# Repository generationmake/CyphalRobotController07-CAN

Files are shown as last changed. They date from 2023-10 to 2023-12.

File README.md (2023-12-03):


CyphalRobotController07/CAN
==================
Main controller board for the T07 robot platform and similar robots with a Raspberry Pi Pico to connect via CAN using OpenCyphal and UCANPHY Micro 

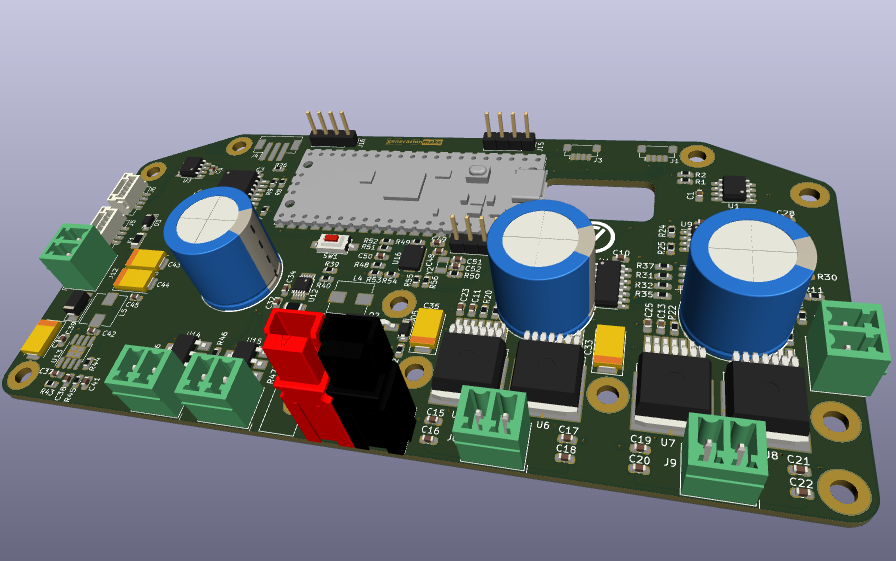
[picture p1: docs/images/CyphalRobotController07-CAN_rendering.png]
CyphalRobotController07/CAN rendering


## features

- power supply for the whole system
  - 5 V for the cyphal network and embedded board (Raspberry Pi or Beagle Bone Black)
  - switchable output of battery voltage to supply additional hardware
  - switchable output of battery voltage to supply LED or head lamp
  - Input voltage up to 25 V
  - Blade type fuse (ATO fuse)
  - Power Pole connector
  - measurement of input voltage and current with TI INA226
- control 2 DC motors
  - 2 quad encoders for motors
  - emergency stop
  - Infineon IFX007T drivers, up to 40V and 55A
- ~~3 ultra sonic sensors HC-SR04~~ (not implemented yet)
- I2C bus
  - qwiic connector
  - 9 axis IMU Bosch BNO055 via I2C
  - back-EMF measurement with ADS1015
  - EEPROM 24LC64
- serial port for optional GNSS
- Neopixel for status
- CAN with Cyphal support

## Firmware
* [CyphalRobotController07-CAN-firmware](https://github.com/107-systems/CyphalRobotController07-CAN-firmware): This is the default firmware for this board. It enables all basic functions

## Pin Usage

### Raspberry Pi Pico (CN1)

| **Pin** | **Pin Name** | **Signal** | **Direction** | **Description** |
|:---:|:---:|:---:|:---:|:---:|
| 1 | GP0 | UART0_TX | output | reserved for future use (GNSS) |
| 2 | GP1 | UART0_RX | input | reserved for future use (GNSS) |
| 3 | GND | GND | GND | |
| 4 | GP2 | QUAD0 | input | Quad encoder A channel 0 |
| 5 | GP3 | QUAD1 | input | Quad encoder A channel 1 |
| 6 | GP4 | I2C0_SDA | bidir | for eeprom and qwiic connector |
| 7 | GP5 | I2C0_SCL | output | for eeprom and qwiic connector |
| 8 | GND | GND | GND | |
| 9 | GP6 | PWM4 | output | motor pwm output 4 |
| 10 | GP7 | PWM3 | output | motor pwm output 3 |
| 11 | GP8 | PWM2 | output | motor pwm output 2 |
| 12 | GP9 | PWM1 | output | motor pwm output 1 |
| 13 | GND | GND | GND | |
| 14 | GP10 | INH34 | output | motor inhibit output 3 and 4 |
| 15 | GP11 | INH12 | output | motor inhibit output 1 and 2 |
| 16 | GP12 | EM_STOP | input | emergency stop |
| 17 | GP13 | NEOPIXEL | output | Neopixel |
| 18 | GND | GND | GND | |
| 19 | GP14 | QUAD2 | input | Quad encoder B channel 0 |
| 20 | GP15 | QUAD3 | input | Quad encoder B channel 1 |
| 21 | GP16 | SPI_MISO | input | SPI for MCP2515 |
| 22 | GP17 | MCP2515_CS | output | SPI for MCP2515 |
| 23 | GND | GND | GND | |
| 24 | GP18 | SPI_CLK | output | SPI for MCP2515 |
| 25 | GP19 | SPI_MOSI | output | SPI for MCP2515 |
| 26 | GP20 | MCP2515_INT | input | interrupt for MCP2515 |
| 27 | GP21 | OUTPUT0 | output | power output 0 |
| 28 | GND | GND | GND | |
| 29 | GP22 | OUTPUT1 | output | power output 1 |
| 30 | RUN | RESET | input | Reset for Board |
| 31 | GP26 | ANALOG_INPUT0 | analog input  | analog input 0 |
| 32 | GP27 | ANALOG_INPUT1 | analog input  | analog input 1 |
| 33 | GND | GND | GND | |
| 34 | GP28 | ANALOG_INPUT2 | analog input  | analog input 2 |
| 35 | ADC_VREF | | analog | |
| 36 | 3V3 (OUT) | 3V3-rail | power | supply voltage for board |
| 37 | 3V3_EN | | input | |
| 38 | GND | GND | GND | |
| 39 | VSYS | | power | |
| 40 | VBUS | 5V-rail | power | supply voltage for board |

## I2C devices

| address | device  | description |
|---|---|---|
| 0x40 | INA226  | voltage and current measurement |
| 0x48 | ADS1015 | motor measurement |
| 0x4A | BNO055  | IMU |
| 0x50 | 24LC64  | eeprom for storage of settings  |
## PCB

### Top

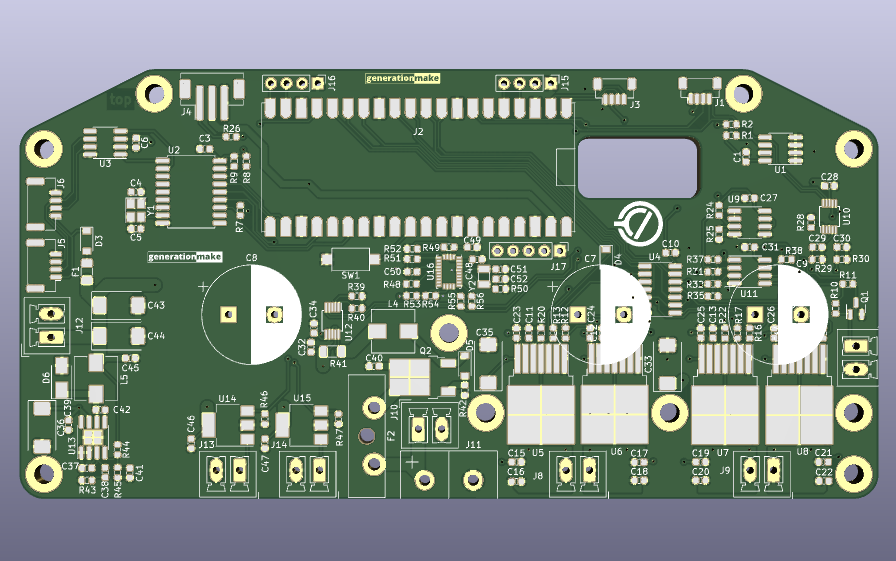
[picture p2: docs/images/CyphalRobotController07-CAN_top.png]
CyphalRobotController07/CAN PCB top


### Bottom

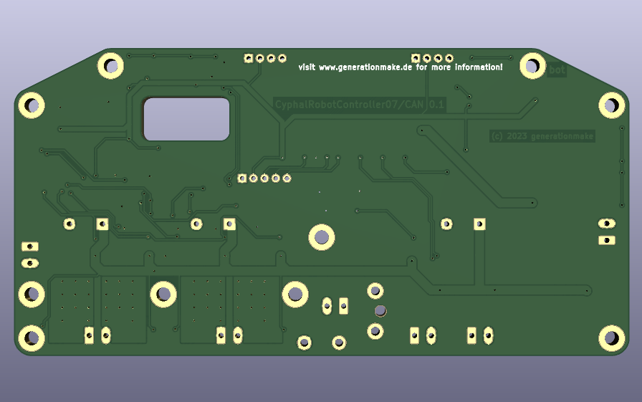
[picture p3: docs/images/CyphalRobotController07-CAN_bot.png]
CyphalRobotController07/CAN PCB bot


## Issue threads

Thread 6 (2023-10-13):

replace tantal capacitors with electrolytic capacitors

generationmake, 2023-10-13:
cheaper and better availability

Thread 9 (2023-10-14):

fix hardware errors of pcb 0.1

generationmake, 2023-10-14:

generationmake, 2023-10-15:
connect both 3.3 v rails

generationmake, 2023-10-15:
add weak pull down (100k) on EM_STOP_D

generationmake, 2023-11-16:
add always on output for battery voltage to connect external controller board

Closed 2025-09-04.

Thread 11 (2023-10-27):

Feature Request: Adjust footprint to allow usage Rasperry Pi Pico w/ Pin Headers (RP  PICO H)

aentinger, 2023-10-27:
See this [one](https://www.conrad.at/de/p/raspberry-pi-rp-pico-h-mikrocontroller-rp-pico-h-2615362.html).

I mistakenly ordered 20 pieces of that one ... 🤦

Closed 2025-09-04.

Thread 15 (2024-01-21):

update input voltage to 40 V

generationmake, 2024-01-21:
to allow usage of 40 V power tool batteries or 2x 20 V in series

generationmake, 2024-01-21:
replace INA226
check capacitors

generationmake, 2024-01-21:
replace ITS4200S

generationmake, 2024-01-21:
replace IPD90P03P4L-04 with IPD90P04P4L-04

Closed 2025-09-04.

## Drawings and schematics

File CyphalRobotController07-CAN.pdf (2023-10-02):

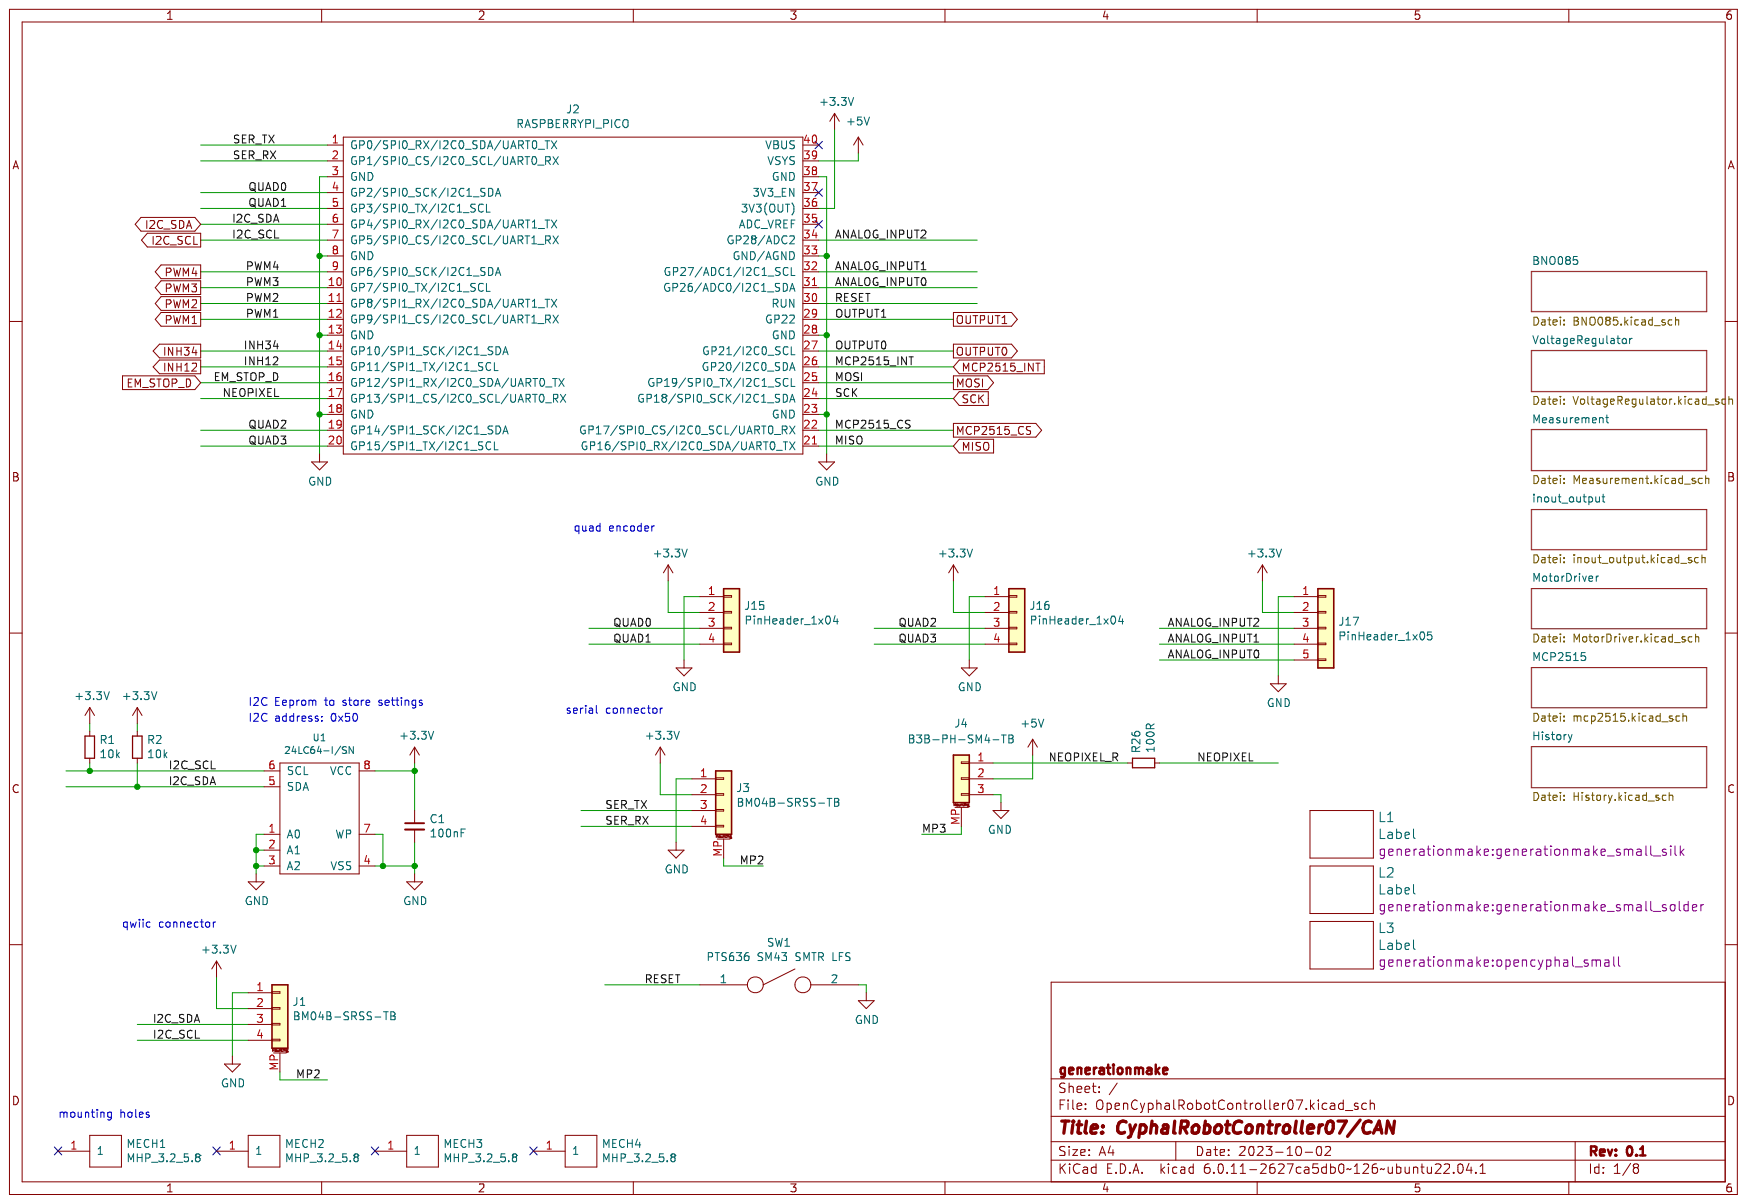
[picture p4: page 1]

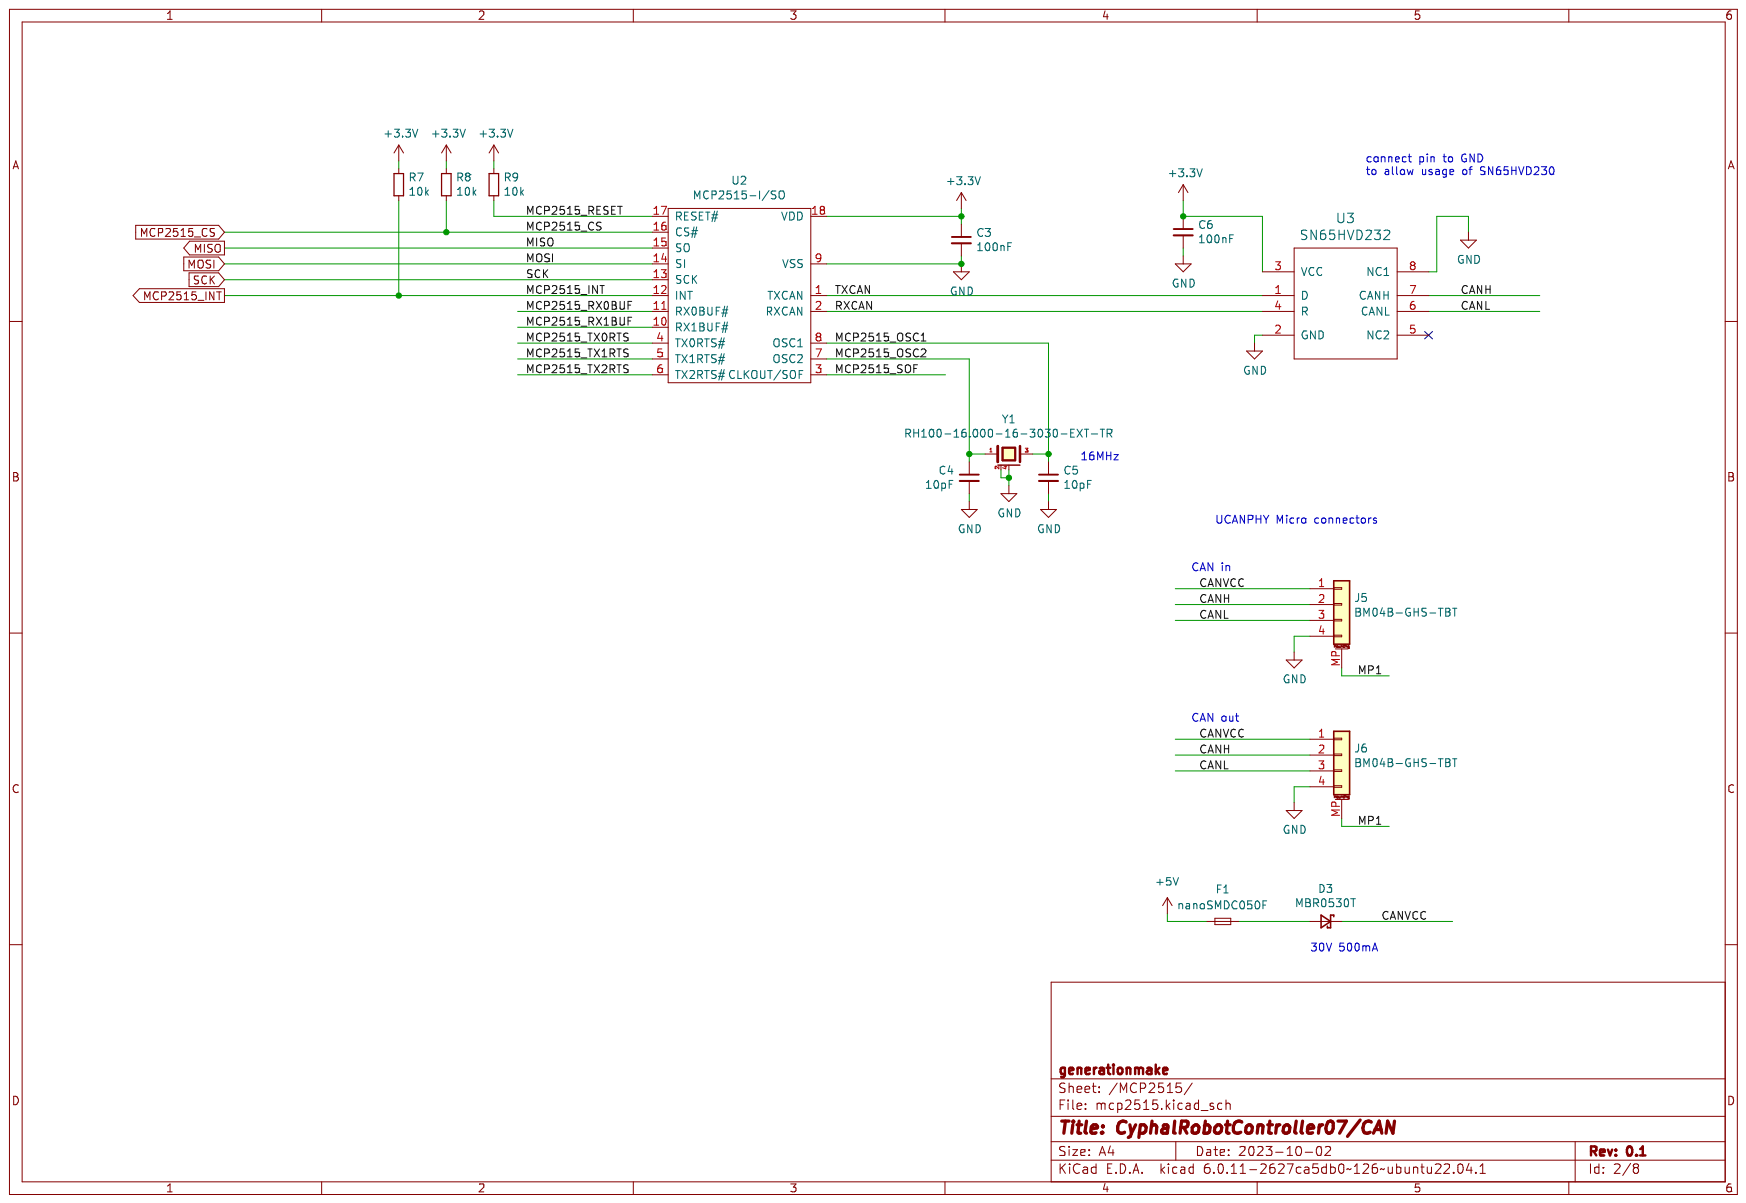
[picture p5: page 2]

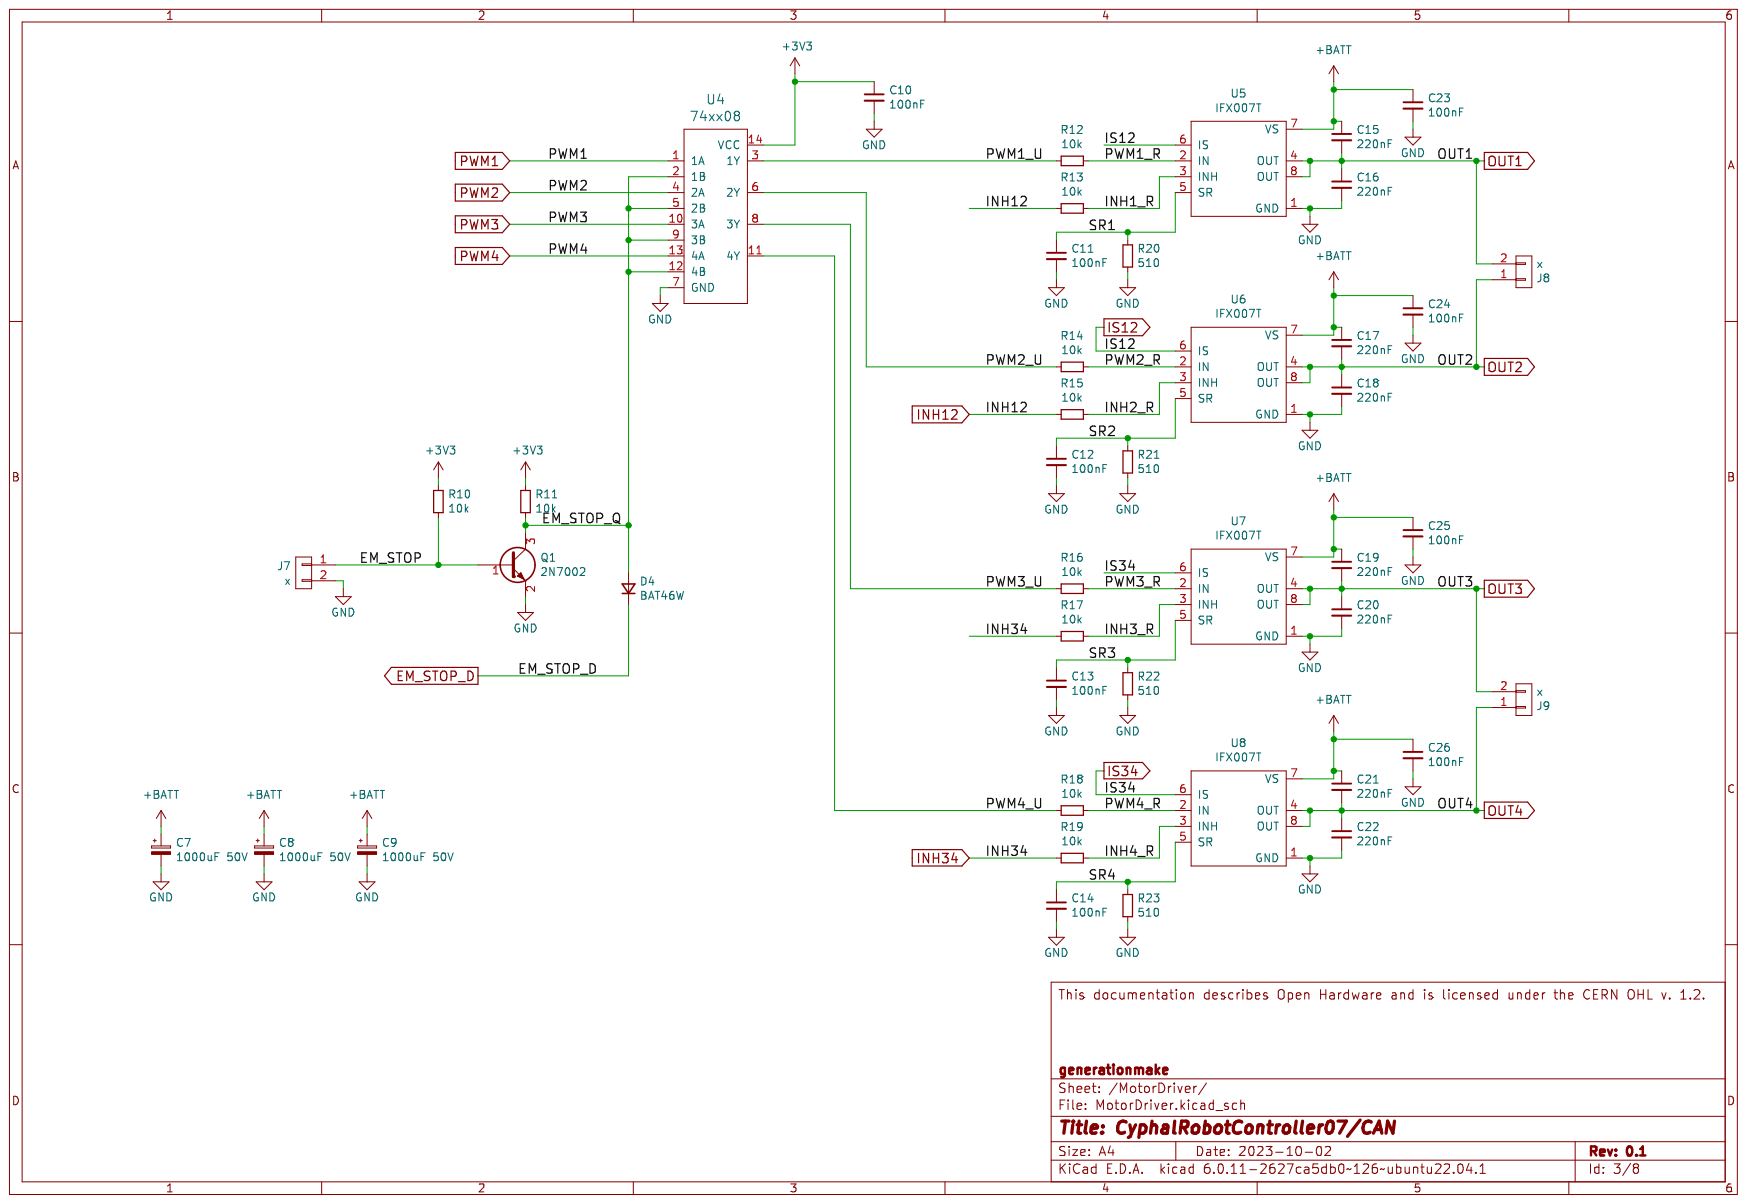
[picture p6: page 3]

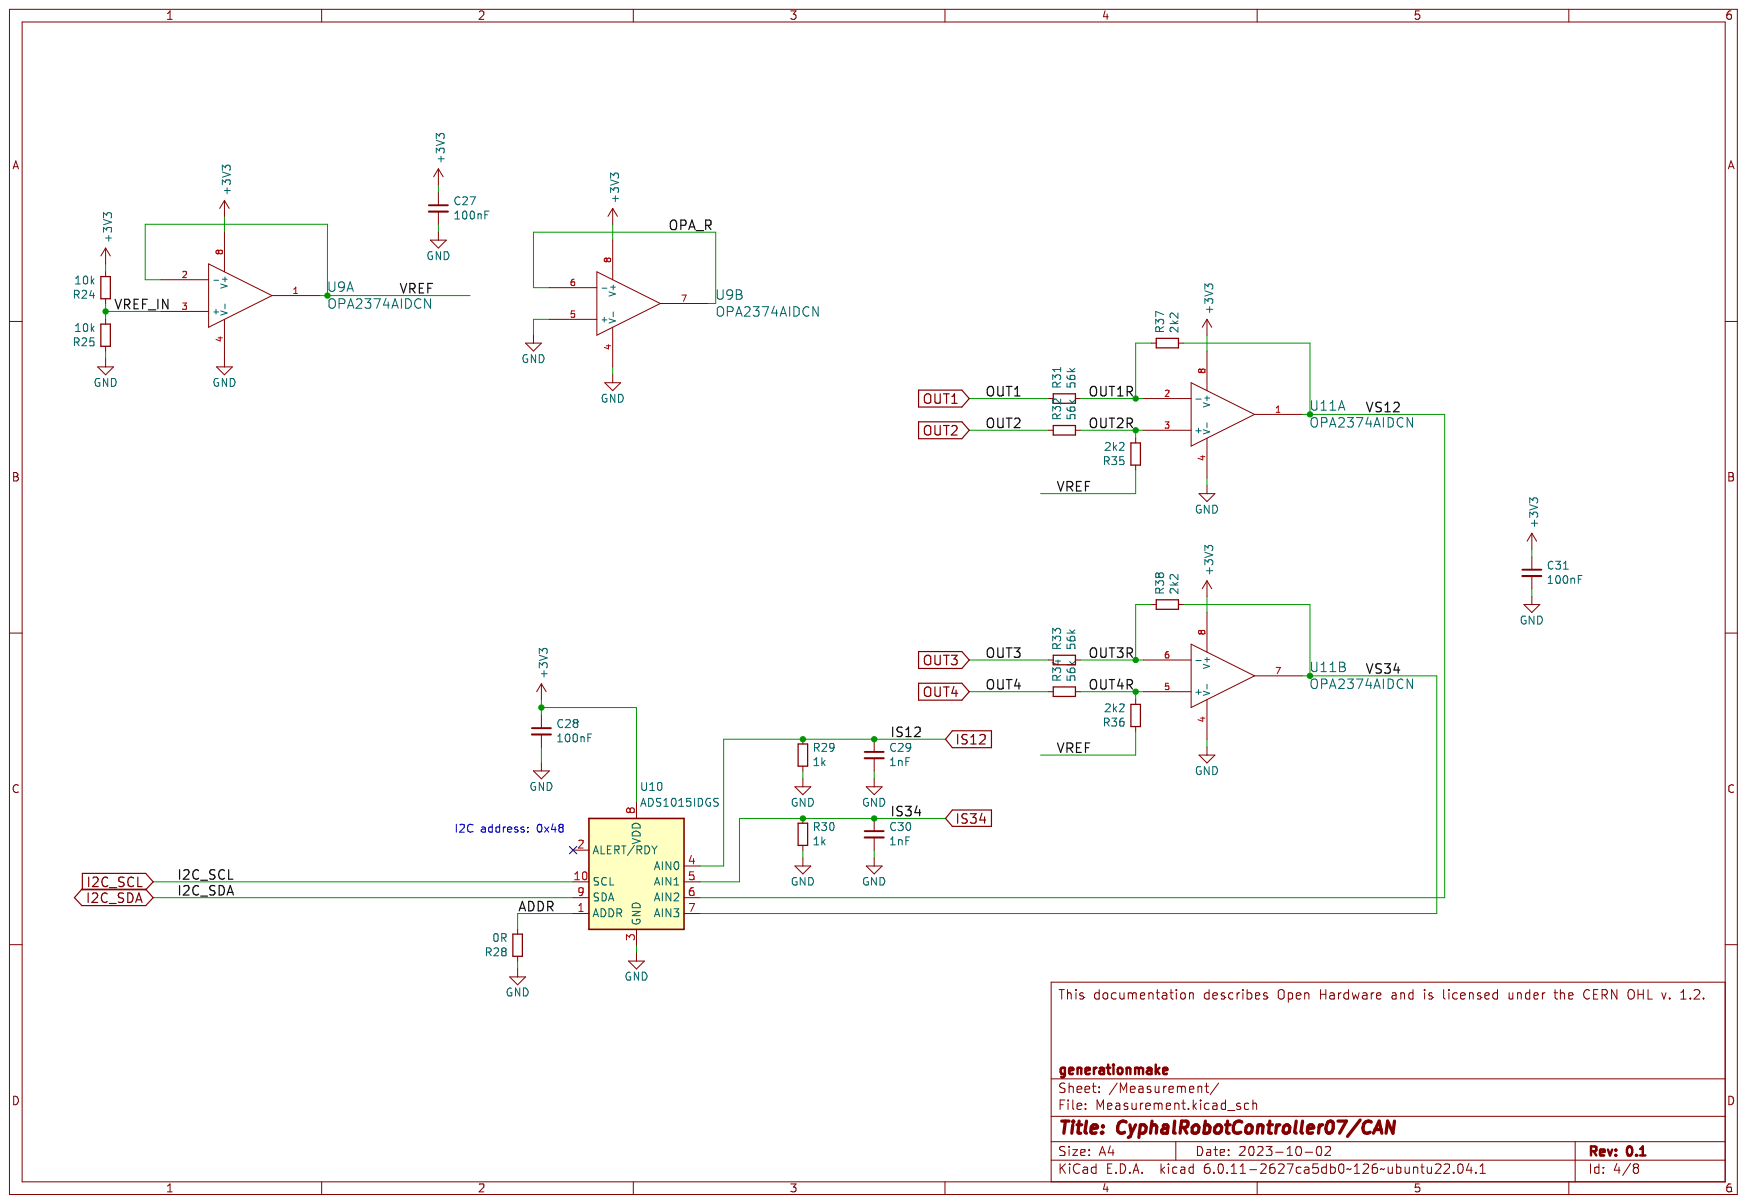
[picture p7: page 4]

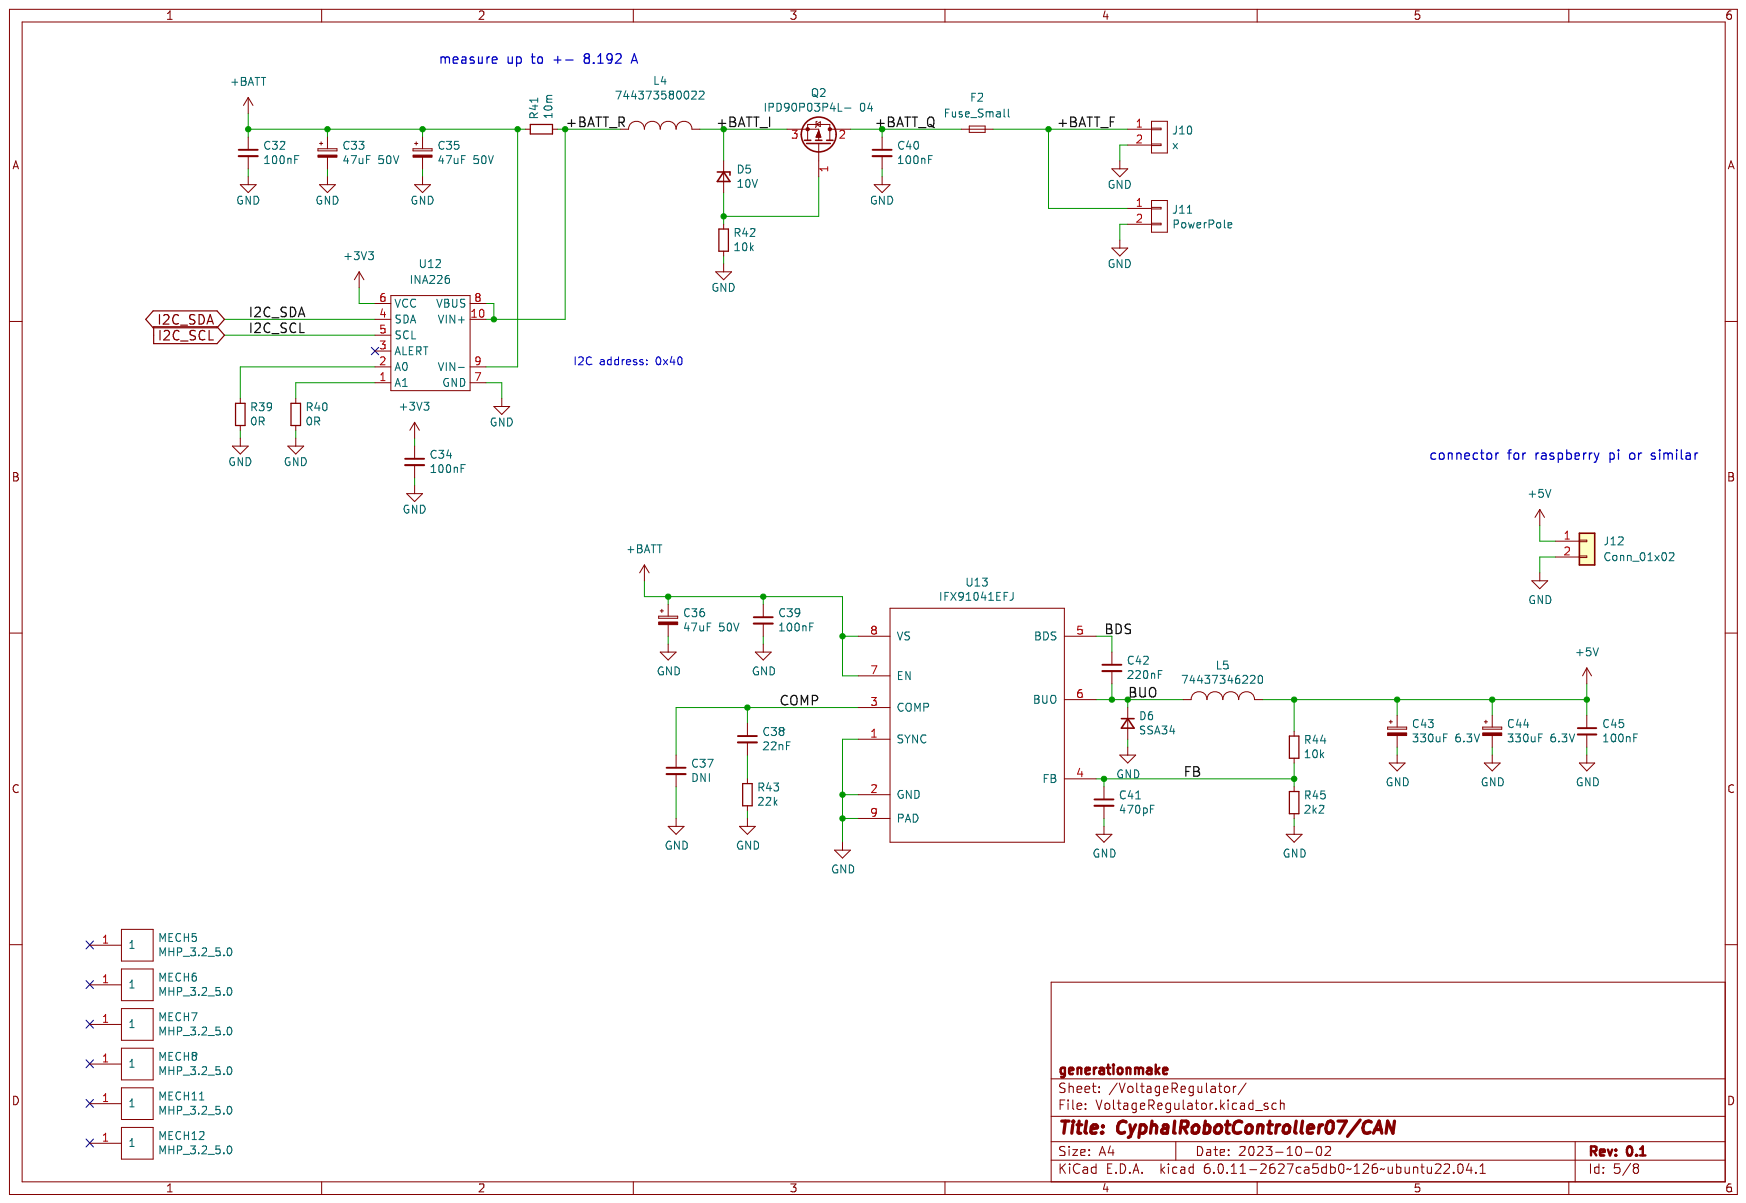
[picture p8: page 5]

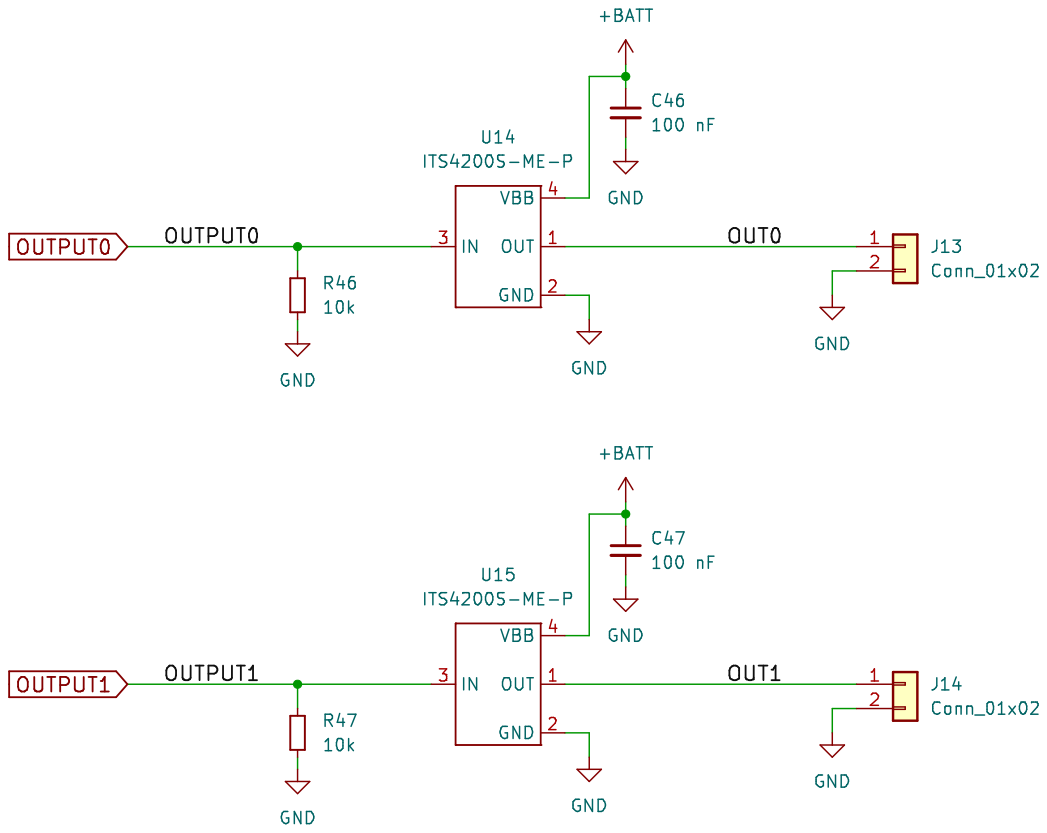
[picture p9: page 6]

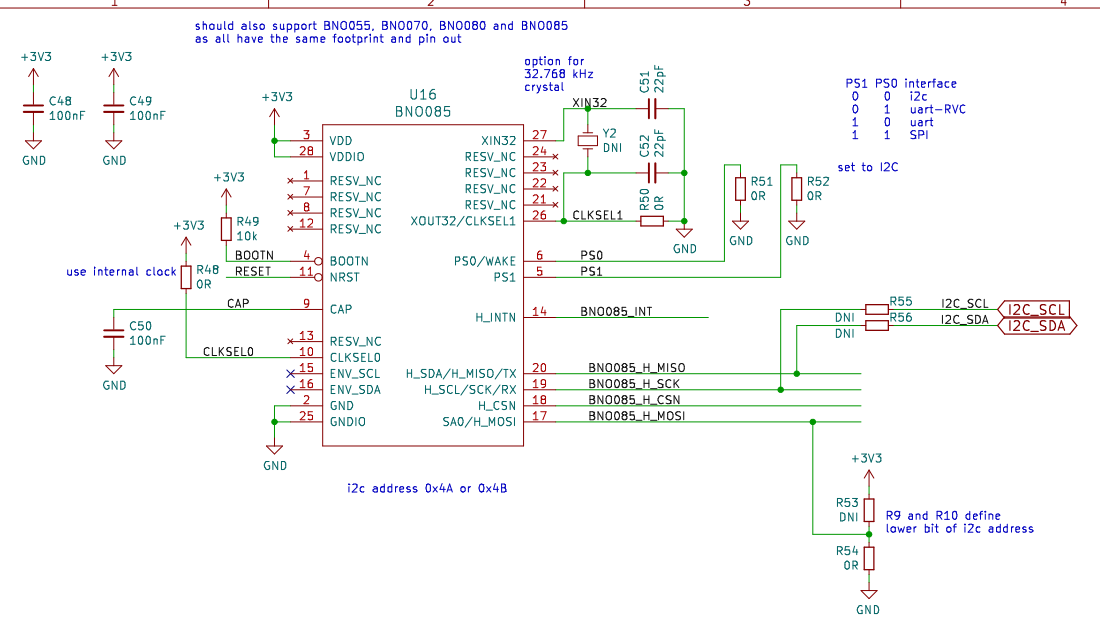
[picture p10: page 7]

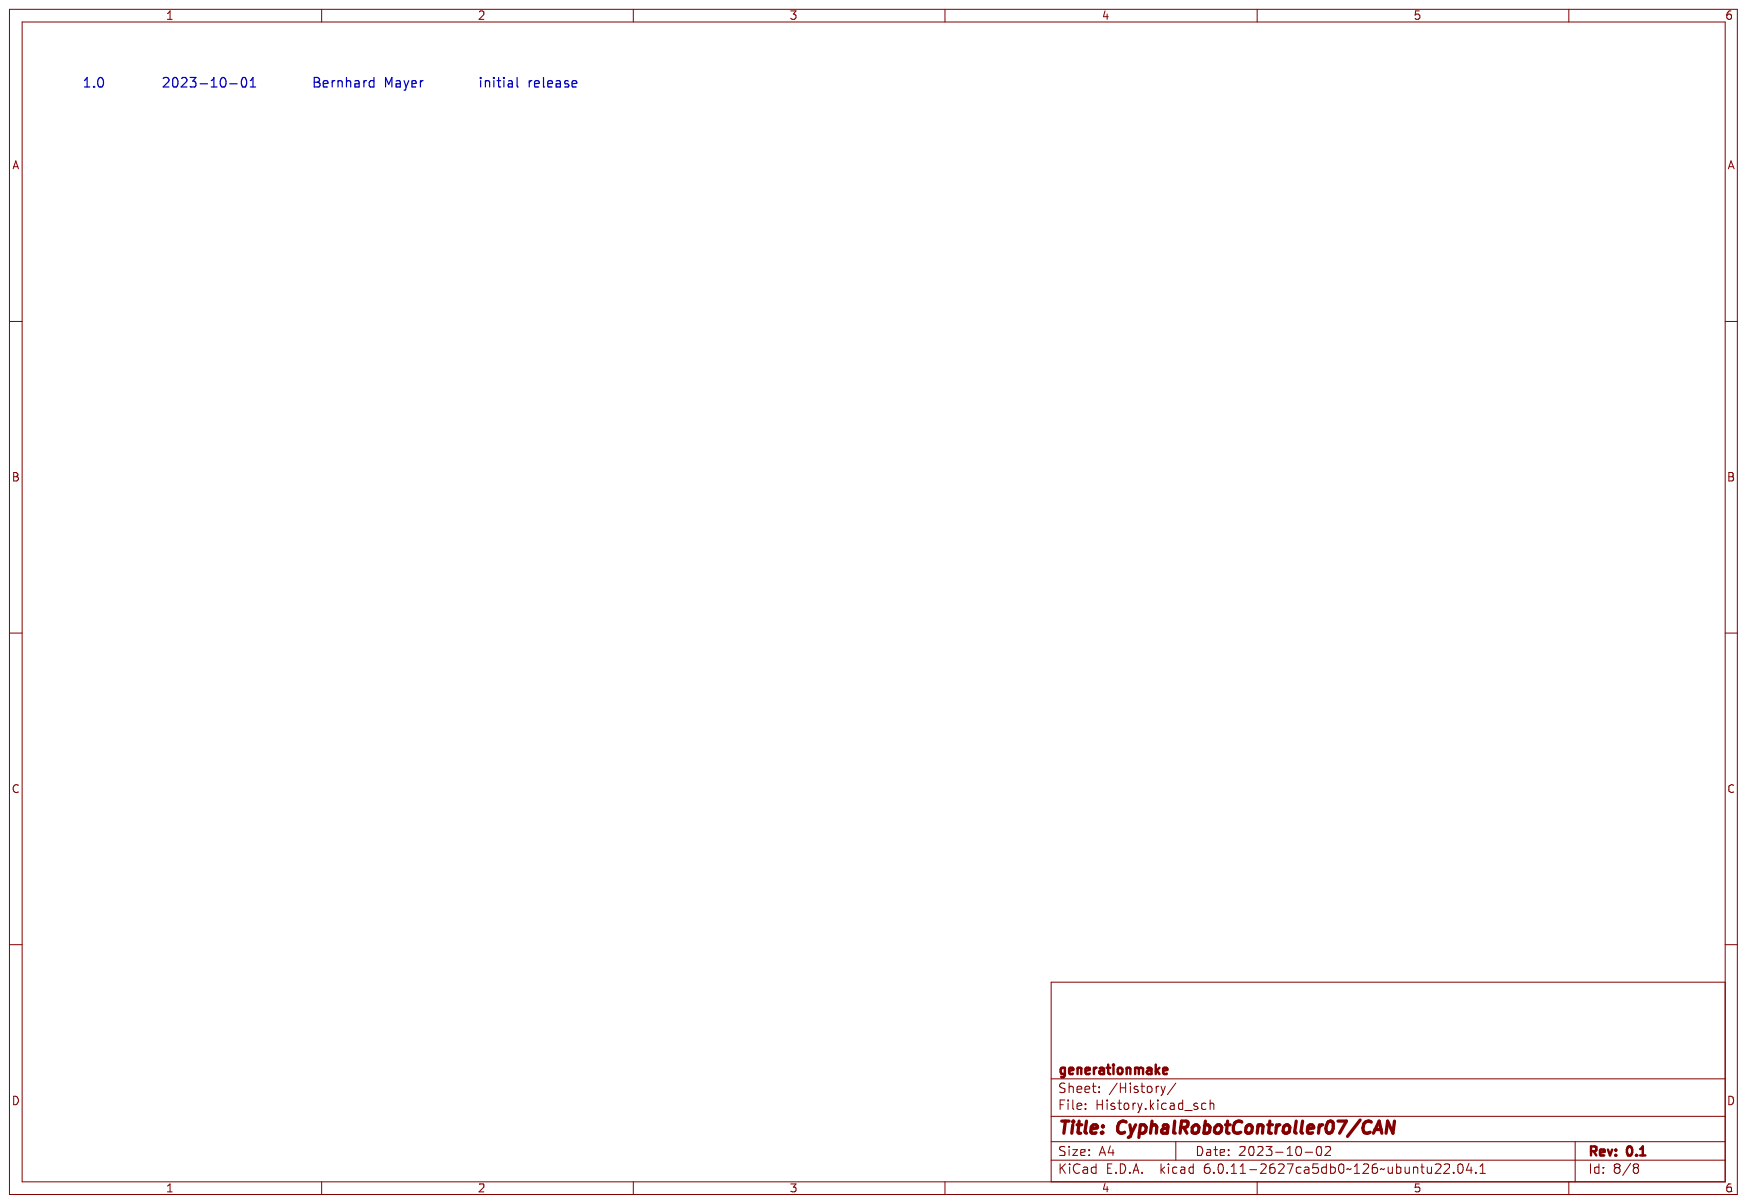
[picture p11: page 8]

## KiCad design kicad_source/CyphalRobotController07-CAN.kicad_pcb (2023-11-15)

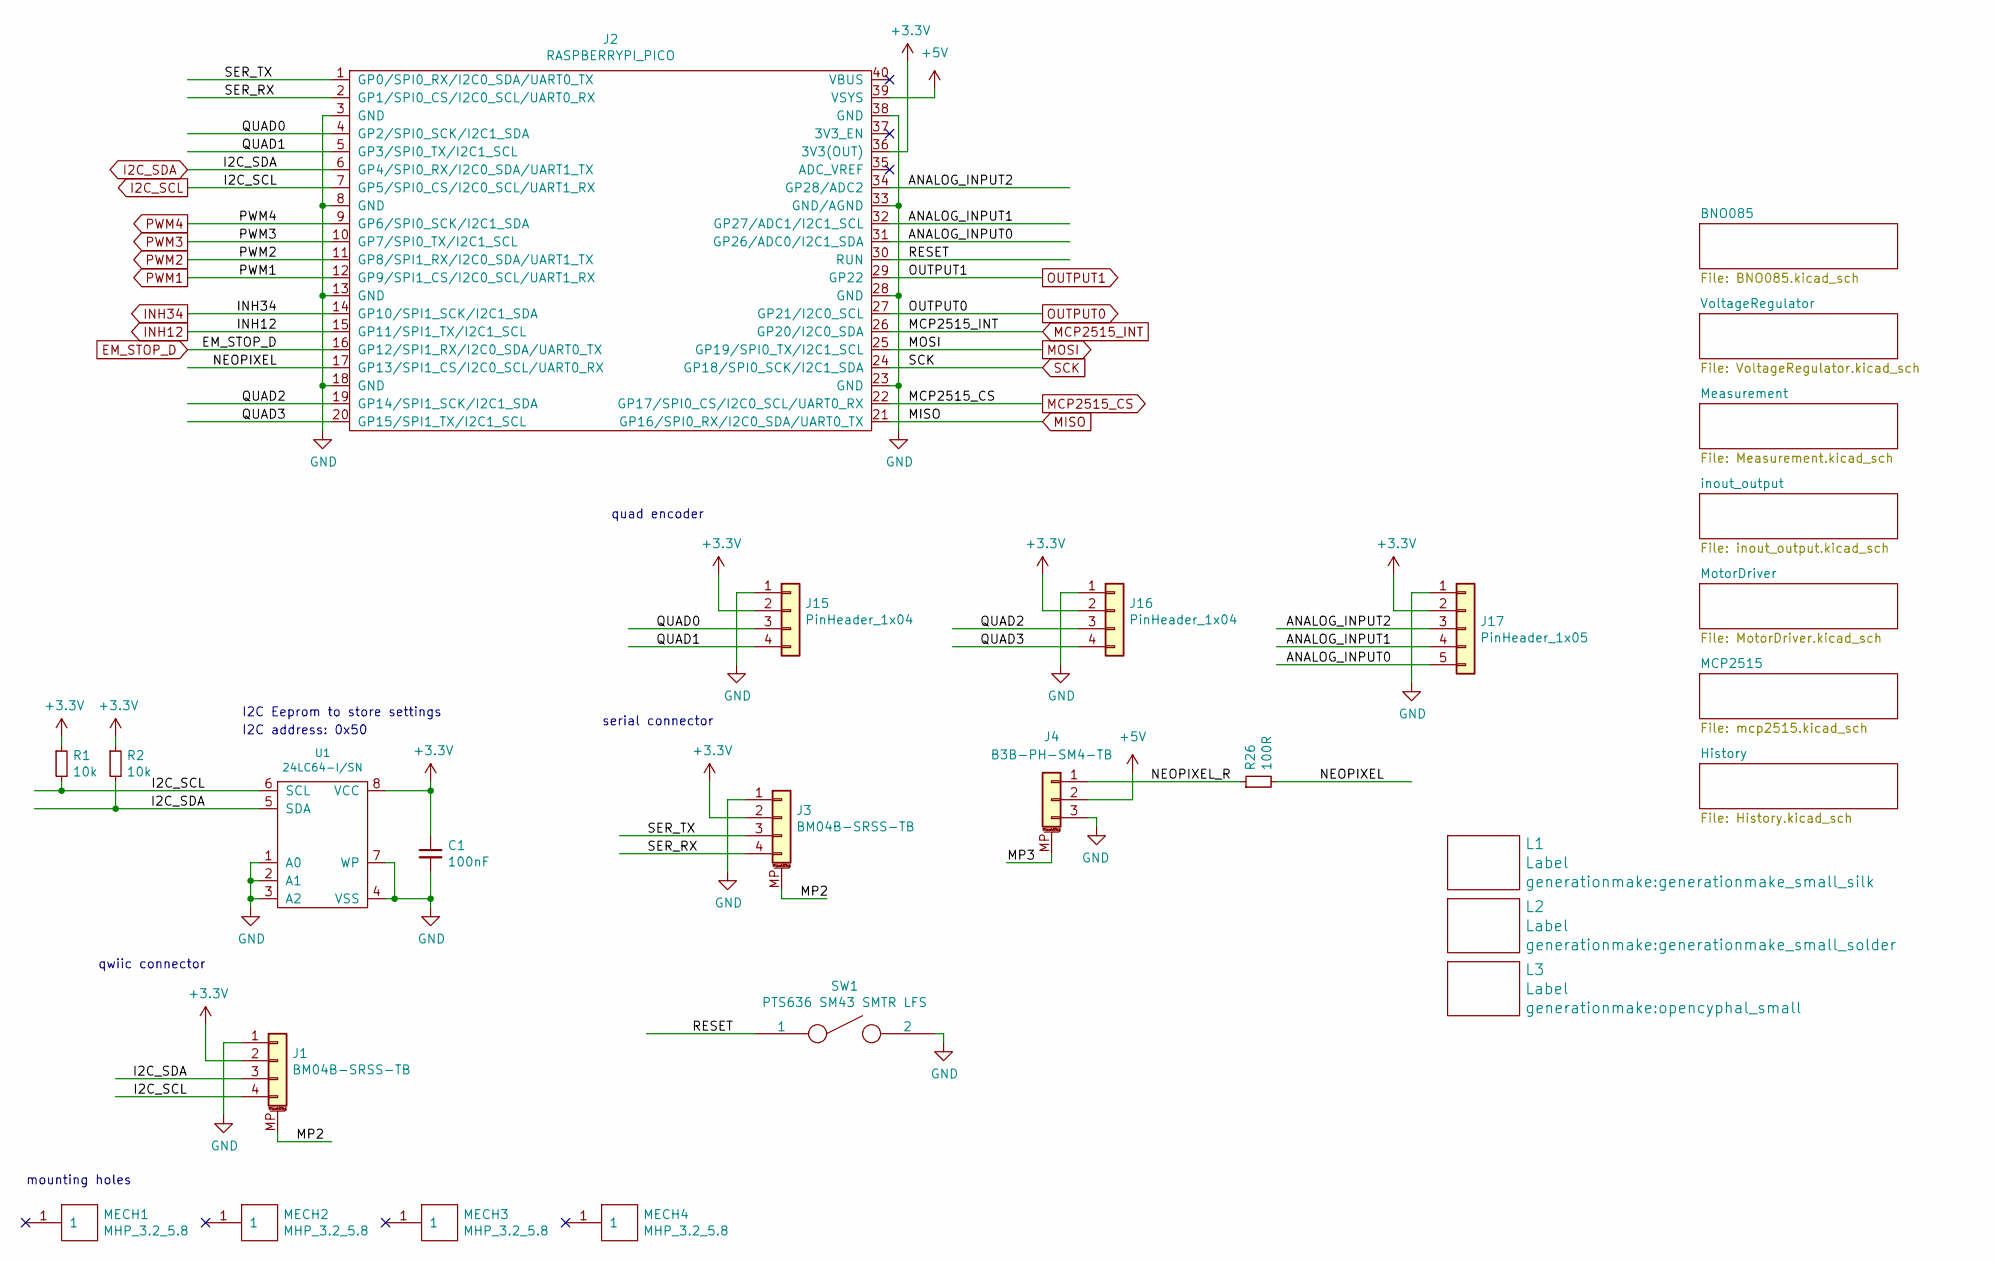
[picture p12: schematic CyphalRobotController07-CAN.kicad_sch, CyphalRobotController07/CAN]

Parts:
C1: 100nF; C_0603_1608Metric
J1, J3: BM04B-SRSS-TB; JST_SH_BM04B-SRSS-TB_1x04-1MP_P1.00mm_Vertical
J2: RASPBERRYPI_PICO; RASPI_PICO_SOLDER_Kopie
J4: B3B-PH-SM4-TB; JST_PH_B3B-PH-SM4-TB_1x03-1MP_P2.00mm_Vertical
J15, J16: PinHeader_1x04; PinHeader_1x04_P2.54mm_Vertical
J17: PinHeader_1x05; PinHeader_1x05_P2.54mm_Vertical
L1: Label; generationmake_small_silk
L2: Label; generationmake_small_solder
L3: Label; opencyphal_small
MECH1, MECH2, MECH3, MECH4: MHP_3.2_5.8
R1, R2: 10k; R_0603_1608Metric
R26: 100R; R_0603_1608Metric
SW1: PTS636 SM43 SMTR LFS; SW_SPST_CK_RS282G05A3
U1: 24LC64-I/SN; SOIC-8_3.9x4.9mm_P1.27mm

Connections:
+5V: J2.39 (VSYS), J4.2; also elsewhere on the board
/ANALOG_INPUT0: J2.31 (GP26/ADC0/I2C1_SDA), J17.5
/ANALOG_INPUT1: J2.32 (GP27/ADC1/I2C1_SCL), J17.4
/ANALOG_INPUT2: J2.34 (GP28/ADC2), J17.3
/MP2: J1.MP (MountPin), J3.MP (MountPin)
/MP3: J4.MP (MountPin)
/NEOPIXEL: J2.17 (GP13/SPI1_CS/I2C0_SCL/UART0_RX), R26.2
/NEOPIXEL_R: J4.1, R26.1
/QUAD0: J2.4 (GP2/SPI0_SCK/I2C1_SDA), J15.3
/QUAD1: J2.5 (GP3/SPI0_TX/I2C1_SCL), J15.4
/QUAD2: J2.19 (GP14/SPI1_SCK/I2C1_SDA), J16.3
/QUAD3: J2.20 (GP15/SPI1_TX/I2C1_SCL), J16.4
/RESET: J2.30 (RUN), SW1.1
/SER_RX: J2.2 (GP1/SPI0_CS/I2C0_SCL/UART0_RX), J3.4
/SER_TX: J2.1 (GP0/SPI0_RX/I2C0_SDA/UART0_TX), J3.3
EM_STOP_D: J2.16 (GP12/SPI1_RX/I2C0_SDA/UART0_TX); also elsewhere on the board
GND: C1.2, J1.1, J2.3 (GND), J2.8 (GND), J2.13 (GND), J2.18 (GND), J2.23 (GND), J2.28 (GND), J2.33 (GND/AGND), J2.38 (GND), J3.1, J4.3, J15.1, J16.1, J17.1, SW1.2, U1.1 (A0), U1.2 (A1), U1.3 (A2), U1.4 (VSS), U1.7 (WP); also elsewhere on the board
I2C_SCL: J1.4, J2.7 (GP5/SPI0_CS/I2C0_SCL/UART1_RX), R1.2, U1.6 (SCL); also elsewhere on the board
I2C_SDA: J1.3, J2.6 (GP4/SPI0_RX/I2C0_SDA/UART1_TX), R2.2, U1.5 (SDA); also elsewhere on the board
INH12: J2.15 (GP11/SPI1_TX/I2C1_SCL); also elsewhere on the board
INH34: J2.14 (GP10/SPI1_SCK/I2C1_SDA); also elsewhere on the board
MCP2515_CS: J2.22 (GP17/SPI0_CS/I2C0_SCL/UART0_RX); also elsewhere on the board
MCP2515_INT: J2.26 (GP20/I2C0_SDA); also elsewhere on the board
MISO: J2.21 (GP16/SPI0_RX/I2C0_SDA/UART0_TX); also elsewhere on the board
MOSI: J2.25 (GP19/SPI0_TX/I2C1_SCL); also elsewhere on the board
OUTPUT0: J2.27 (GP21/I2C0_SCL); also elsewhere on the board
OUTPUT1: J2.29 (GP22); also elsewhere on the board
PWM1: J2.12 (GP9/SPI1_CS/I2C0_SCL/UART1_RX); also elsewhere on the board
PWM2: J2.11 (GP8/SPI1_RX/I2C0_SDA/UART1_TX); also elsewhere on the board
PWM3: J2.10 (GP7/SPI0_TX/I2C1_SCL); also elsewhere on the board
PWM4: J2.9 (GP6/SPI0_SCK/I2C1_SDA); also elsewhere on the board
SCK: J2.24 (GP18/SPI0_SCK/I2C1_SDA); also elsewhere on the board

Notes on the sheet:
quad encoder
serial connector
qwiic connector
mounting holes
I2C address: 0x50
I2C Eeprom to store settings

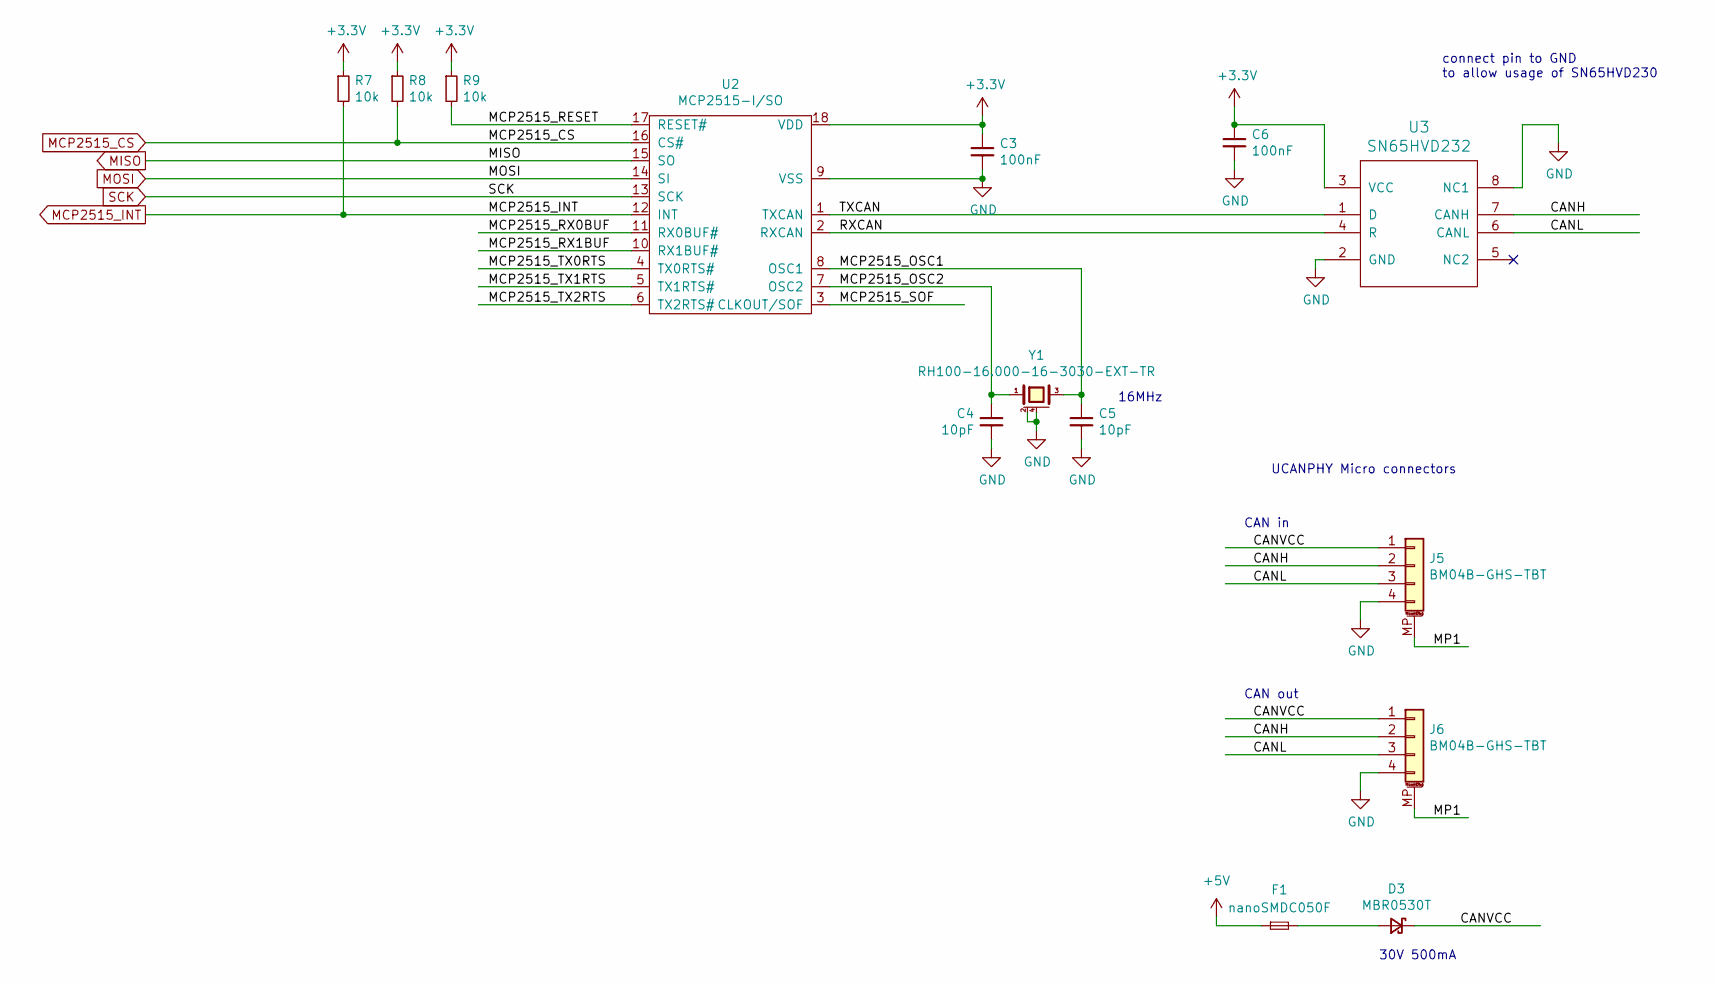
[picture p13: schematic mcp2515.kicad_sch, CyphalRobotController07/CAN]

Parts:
C3, C6: 100nF; C_0603_1608Metric
C4, C5: 10pF; C_0603_1608Metric
D3: MBR0530T; D_SOD-123
F1: nanoSMDC050F; Fuse_1206_3216Metric
J5, J6: BM04B-GHS-TBT; JST_GH_BM04B-GHS-TBT_1x04-1MP_P1.25mm_Vertical
R7, R8, R9: 10k; R_0603_1608Metric
U2: MCP2515-I/SO; SOIC-18W_7.5x11.6mm_P1.27mm
U3: SN65HVD232; SOIC-8_3.9x4.9mm_P1.27mm
Y1: RH100-16.000-16-3030-EXT-TR; Crystal_SMD_3225-4Pin_3.2x2.5mm

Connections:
+5V: F1.1; also elsewhere on the board
/MCP2515/CANH: J5.2, J6.2, U3.7 (CANH)
/MCP2515/CANL: J5.3, J6.3, U3.6 (CANL)
/MCP2515/CANVCC: D3.1 (K), J5.1, J6.1
/MCP2515/MCP2515_OSC1: C5.1, U2.8 (OSC1), Y1.3
/MCP2515/MCP2515_OSC2: C4.1, U2.7 (OSC2), Y1.1
/MCP2515/MCP2515_RESET: R9.2, U2.17 (RESET#)
/MCP2515/MCP2515_RX0BUF: U2.11 (RX0BUF#)
/MCP2515/MCP2515_RX1BUF: U2.10 (RX1BUF#)
/MCP2515/MCP2515_SOF: U2.3 (CLKOUT/SOF)
/MCP2515/MCP2515_TX0RTS: U2.4 (TX0RTS#)
/MCP2515/MCP2515_TX1RTS: U2.5 (TX1RTS#)
/MCP2515/MCP2515_TX2RTS: U2.6 (TX2RTS#)
/MCP2515/MP1: J5.MP (MountPin), J6.MP (MountPin)
/MCP2515/RXCAN: U2.2 (RXCAN), U3.4 (R)
/MCP2515/TXCAN: U2.1 (TXCAN), U3.1 (D)
GND: C3.2, C4.2, C5.2, C6.2, J5.4, J6.4, U2.9 (VSS), U3.2 (GND), U3.8 (NC1), Y1.2 (case), Y1.4 (case); also elsewhere on the board
MCP2515_CS: R8.2, U2.16 (CS#); also elsewhere on the board
MCP2515_INT: R7.2, U2.12 (INT); also elsewhere on the board
MISO: U2.15 (SO); also elsewhere on the board
MOSI: U2.14 (SI); also elsewhere on the board
unnamed: D3.2 (A), F1.2
SCK: U2.13 (SCK); also elsewhere on the board

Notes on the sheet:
16MHz
connect pin to GND to allow usage of SN65HVD230
UCANPHY Micro connectors
30V 500mA
CAN in
CAN out

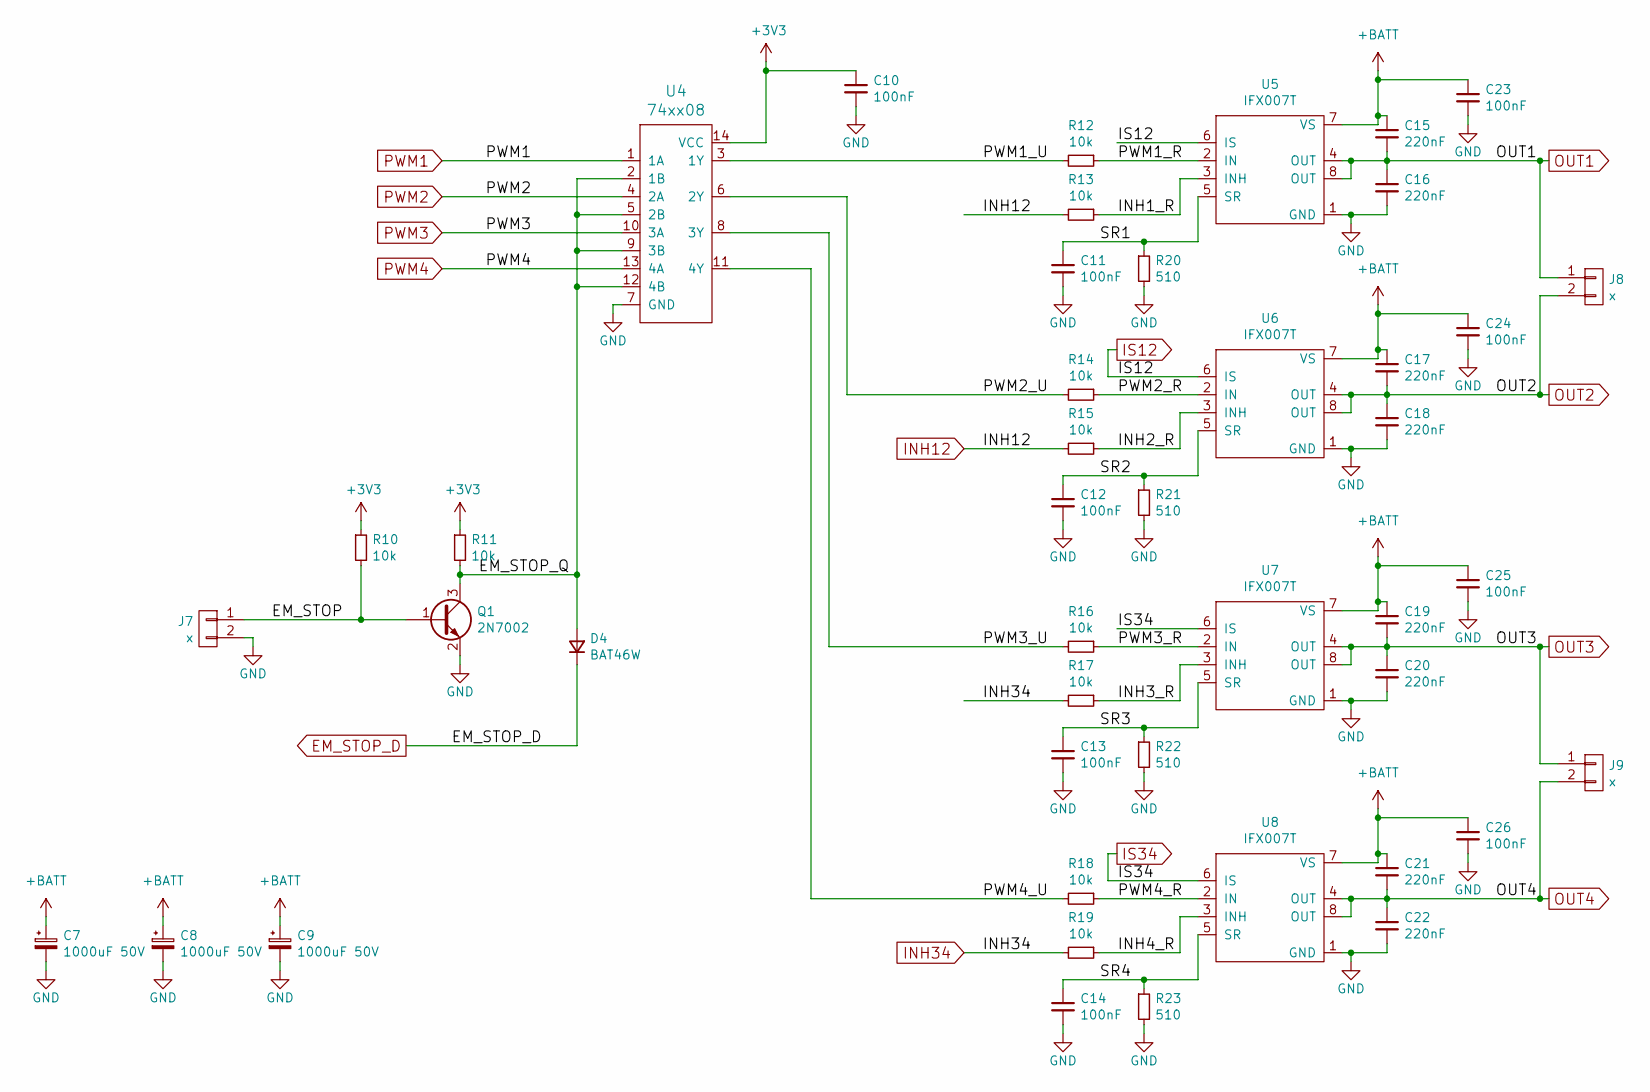
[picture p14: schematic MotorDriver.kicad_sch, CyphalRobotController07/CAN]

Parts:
C7, C8, C9: 1000uF 50V; CP_Radial_D16.0mm_P7.50mm
C10, C11, C12, C13, C14, C23, C24, C25, C26: 100nF; C_0603_1608Metric
C15, C16, C17, C18, C19, C20, C21, C22: 220nF; C_0603_1608Metric
D4: BAT46W; D_SOD-123
J7: x; PhoenixContact_MCV_1,5_2-G-3.81_1x02_P3.81mm_Vertical
J8, J9: x; PhoenixContact_MC_1,5_2-G-3.81_1x02_P3.81mm_Horizontal
Q1: 2N7002; SOT-23
R10, R11, R12, R13, R14, R15, R16, R17, R18, R19: 10k; R_0603_1608Metric
R20, R21, R22, R23: 510; R_0603_1608Metric
U4: 74xx08; SOIC-14_3.9x8.7mm_P1.27mm
U5, U6, U7, U8: IFX007T; TO-263-7_TabPin8

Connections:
+BATT: C7.1, C8.1, C9.1, C15.1, C17.1, C19.1, C21.1, C23.1, C24.1, C25.1, C26.1, U5.7 (VS), U6.7 (VS), U7.7 (VS), U8.7 (VS); also elsewhere on the board
/MotorDriver/EM_STOP: J7.1, Q1.1 (B), R10.2
/MotorDriver/EM_STOP_Q: D4.2 (A), Q1.3 (C), R11.2, U4.2 (1B), U4.5 (2B), U4.9 (3B), U4.12 (4B)
/MotorDriver/INH1_R: R13.1, U5.3 (INH)
/MotorDriver/INH2_R: R15.1, U6.3 (INH)
/MotorDriver/INH3_R: R17.1, U7.3 (INH)
/MotorDriver/INH4_R: R19.1, U8.3 (INH)
/MotorDriver/PWM1_R: R12.1, U5.2 (IN)
/MotorDriver/PWM1_U: R12.2, U4.3 (1Y)
/MotorDriver/PWM2_R: R14.1, U6.2 (IN)
/MotorDriver/PWM2_U: R14.2, U4.6 (2Y)
/MotorDriver/PWM3_R: R16.1, U7.2 (IN)
/MotorDriver/PWM3_U: R16.2, U4.8 (3Y)
/MotorDriver/PWM4_R: R18.1, U8.2 (IN)
/MotorDriver/PWM4_U: R18.2, U4.11 (4Y)
/MotorDriver/SR1: C11.1, R20.1, U5.5 (SR)
/MotorDriver/SR2: C12.1, R21.1, U6.5 (SR)
/MotorDriver/SR3: C13.1, R22.1, U7.5 (SR)
/MotorDriver/SR4: C14.1, R23.1, U8.5 (SR)
EM_STOP_D: D4.1 (K); also elsewhere on the board
GND: C7.2, C8.2, C9.2, C10.2, C11.2, C12.2, C13.2, C14.2, C16.2, C18.2, C20.2, C22.2, C23.2, C24.2, C25.2, C26.2, J7.2, Q1.2 (E), R20.2, R21.2, R22.2, R23.2, U4.7 (GND), U5.1 (GND), U6.1 (GND), U7.1 (GND), U8.1 (GND); also elsewhere on the board
INH12: R13.2, R15.2; also elsewhere on the board
INH34: R17.2, R19.2; also elsewhere on the board
IS12: U5.6 (IS), U6.6 (IS); also elsewhere on the board
IS34: U7.6 (IS), U8.6 (IS); also elsewhere on the board
OUT1: C15.2, C16.1, J8.1, U5.4 (OUT), U5.8 (OUT); also elsewhere on the board
OUT2: C17.2, C18.1, J8.2, U6.4 (OUT), U6.8 (OUT); also elsewhere on the board
OUT3: C19.2, C20.1, J9.1, U7.4 (OUT), U7.8 (OUT); also elsewhere on the board
OUT4: C21.2, C22.1, J9.2, U8.4 (OUT), U8.8 (OUT); also elsewhere on the board
PWM1: U4.1 (1A); also elsewhere on the board
PWM2: U4.4 (2A); also elsewhere on the board
PWM3: U4.10 (3A); also elsewhere on the board
PWM4: U4.13 (4A); also elsewhere on the board

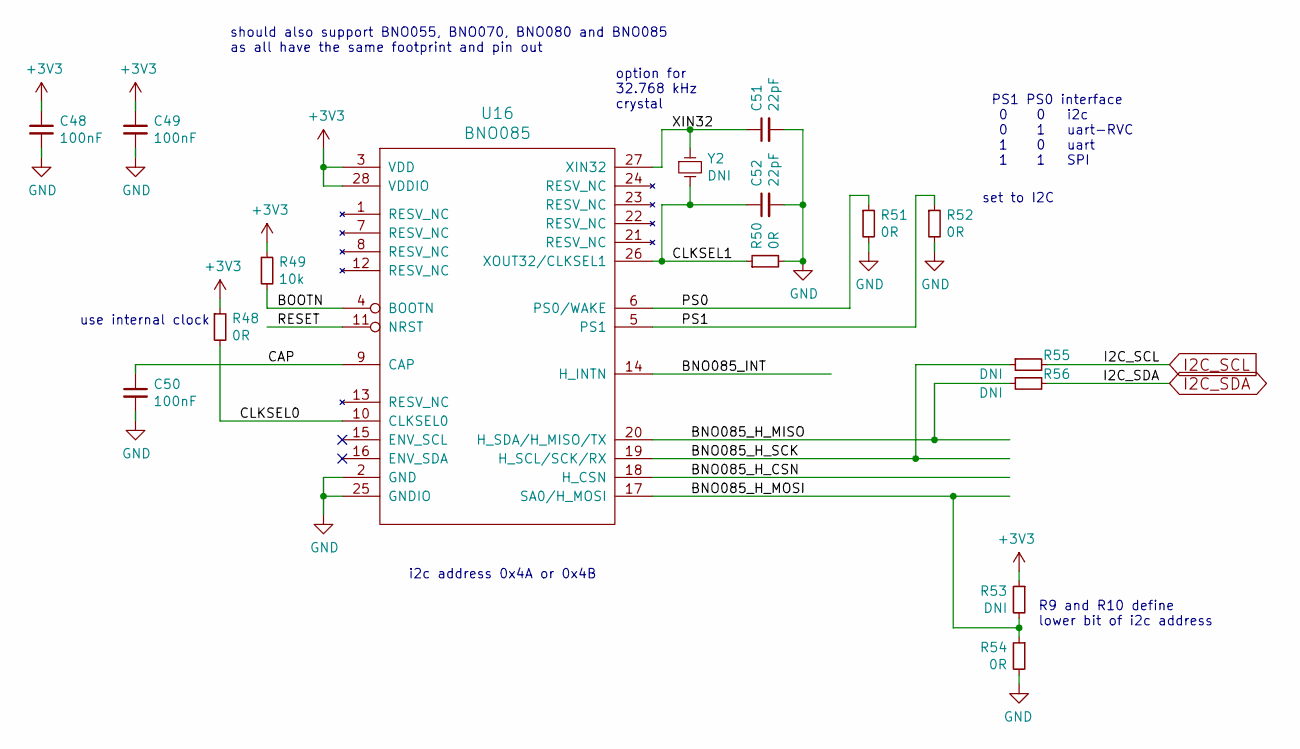
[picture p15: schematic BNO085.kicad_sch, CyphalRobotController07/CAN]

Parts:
C48, C49, C50: 100nF; C_0603_1608Metric
C51, C52: 22pF; C_0603_1608Metric
R48, R50, R51, R52, R54: 0R; R_0603_1608Metric
R49: 10k; R_0603_1608Metric
R53, R55, R56: DNI; R_0603_1608Metric
U16: BNO085; LGA-28_5.2x3.8mm_P0.5mm
Y2: DNI; Crystal_SMD_3215-2Pin_3.2x1.5mm

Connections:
+3V3: C48.1, C49.1, R48.1, R49.1, R53.1, U16.3 (VDD), U16.28 (VDDIO); also elsewhere on the board
/BNO085/BNO085_H_CSN: U16.18 (H_CSN)
/BNO085/BNO085_H_MISO: R56.1, U16.20 (H_SDA/H_MISO/TX)
/BNO085/BNO085_H_MOSI: R53.2, R54.1, U16.17 (SA0/H_MOSI)
/BNO085/BNO085_H_SCK: R55.1, U16.19 (H_SCL/SCK/RX)
/BNO085/BNO085_INT: U16.14 (H_INTN)
/BNO085/BOOTN: R49.2, U16.4 (BOOTN)
/BNO085/CAP: C50.1, U16.9 (CAP)
/BNO085/CLKSEL0: R48.2, U16.10 (CLKSEL0)
/BNO085/CLKSEL1: C52.1, R50.1, U16.26 (XOUT32/CLKSEL1), Y2.2
/BNO085/PS0: R51.1, U16.6 (PS0/WAKE)
/BNO085/PS1: R52.1, U16.5 (PS1)
/BNO085/RESET: U16.11 (NRST)
/BNO085/XIN32: C51.1, U16.27 (XIN32), Y2.1
GND: C48.2, C49.2, C50.2, C51.2, C52.2, R50.2, R51.2, R52.2, R54.2, U16.2 (GND), U16.25 (GNDIO); also elsewhere on the board
I2C_SCL: R55.2; also elsewhere on the board
I2C_SDA: R56.2; also elsewhere on the board

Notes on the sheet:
should also support BNO055, BNO070, BNO080 and BNO085 as all have the same footprint and pin out
set to I2C
i2c address 0x4A or 0x4B
PS1 PS0 interface 0 0 i2c 0 1 uart-RVC 1 0 uart 1 1 SPI
use internal clock
R9 and R10 define lower bit of i2c address
option for 32.768 kHz crystal

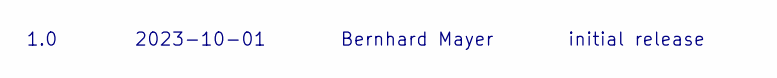
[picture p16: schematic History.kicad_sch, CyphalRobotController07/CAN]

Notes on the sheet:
2023-10-01
1.0
initial release
Bernhard Mayer

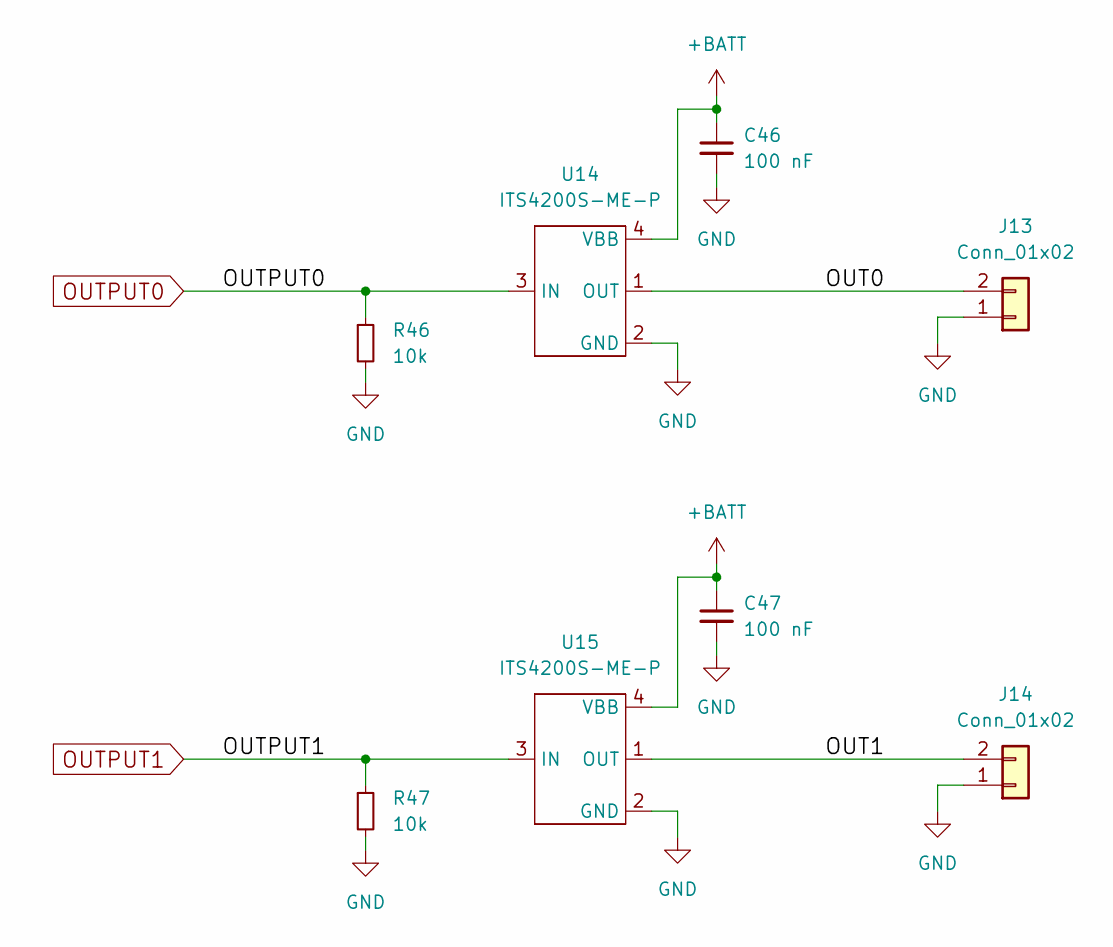
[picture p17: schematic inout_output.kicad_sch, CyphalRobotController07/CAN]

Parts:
C46, C47: 100 nF; C_0603_1608Metric
J13, J14: Conn_01x02; PhoenixContact_MC_1,5_2-G-3.81_1x02_P3.81mm_Horizontal
R46, R47: 10k; R_0603_1608Metric
U14, U15: ITS4200S-ME-P; SOT-223

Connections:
+BATT: C46.1, C47.1, U14.4 (VBB), U15.4 (VBB); also elsewhere on the board
/inout_output/OUT0: J13.2, U14.1 (OUT)
/inout_output/OUT1: J14.2, U15.1 (OUT)
GND: C46.2, C47.2, J13.1, J14.1, R46.2, R47.2, U14.2 (GND), U15.2 (GND); also elsewhere on the board
OUTPUT0: R46.1, U14.3 (IN); also elsewhere on the board
OUTPUT1: R47.1, U15.3 (IN); also elsewhere on the board

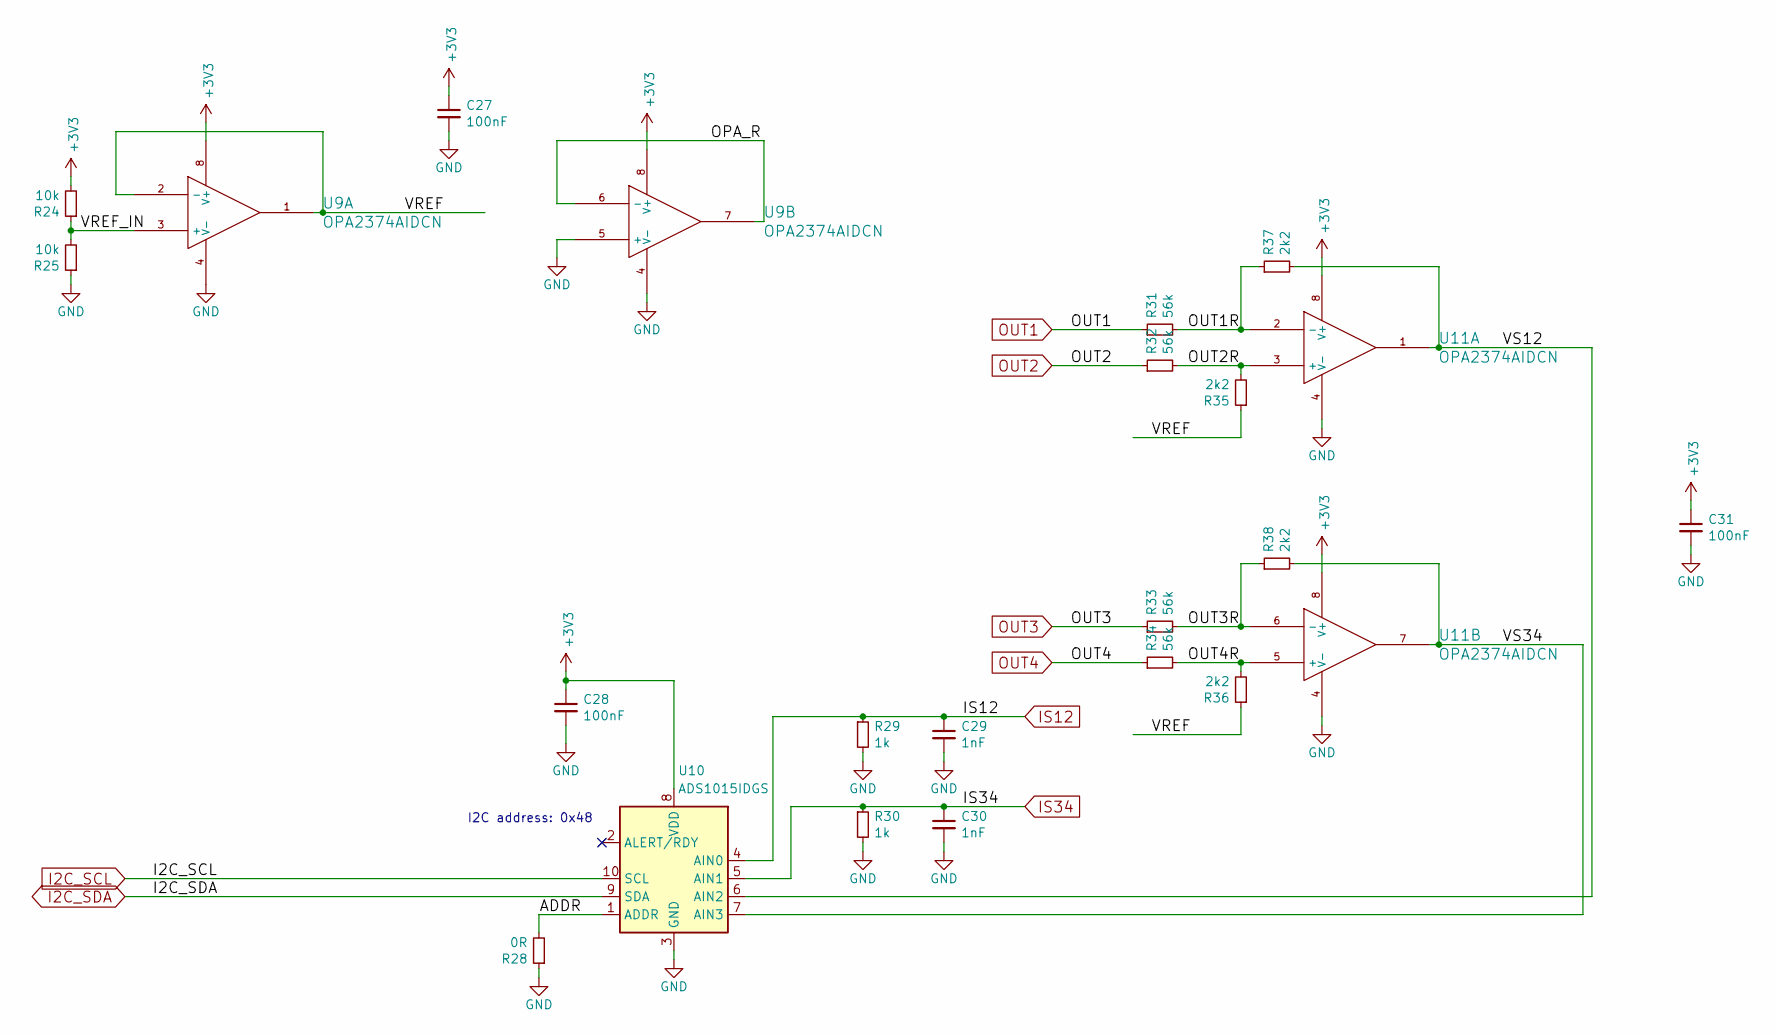
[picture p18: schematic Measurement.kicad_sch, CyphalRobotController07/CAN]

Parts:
C27, C28, C31: 100nF; C_0603_1608Metric
C29, C30: 1nF; C_0603_1608Metric
R24, R25: 10k; R_0603_1608Metric
R28: 0R; R_0603_1608Metric
R29, R30: 1k; R_0603_1608Metric
R31, R32, R33, R34: 56k; R_0603_1608Metric
R35, R36, R37, R38: 2k2; R_0603_1608Metric
U9, U11: OPA2374AIDCN; SOIC-8_3.9x4.9mm_P1.27mm
U10: ADS1015IDGS; TSSOP-10_3x3mm_P0.5mm

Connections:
/Measurement/ADDR: R28.2, U10.1 (ADDR)
/Measurement/OPA_R: U9.6 (-), U9.7
/Measurement/OUT1R: R31.2, R37.1, U11.2 (-)
/Measurement/OUT2R: R32.2, R35.2, U11.3 (+)
/Measurement/OUT3R: R33.2, R38.1, U11.6 (-)
/Measurement/OUT4R: R34.2, R36.2, U11.5 (+)
/Measurement/VREF: R35.1, R36.1, U9.1, U9.2 (-)
/Measurement/VREF_IN: R24.1, R25.2, U9.3 (+)
/Measurement/VS12: R37.2, U10.6 (AIN2), U11.1
/Measurement/VS34: R38.2, U10.7 (AIN3), U11.7
GND: C27.2, C28.2, C29.2, C30.2, C31.2, R25.1, R28.1, R29.2, R30.2, U9.4 (V-), U9.5 (+), U10.3 (GND), U11.4 (V-); also elsewhere on the board
I2C_SCL: U10.10 (SCL); also elsewhere on the board
I2C_SDA: U10.9 (SDA); also elsewhere on the board
IS12: C29.1, R29.1, U10.4 (AIN0); also elsewhere on the board
IS34: C30.1, R30.1, U10.5 (AIN1); also elsewhere on the board
OUT1: R31.1; also elsewhere on the board
OUT2: R32.1; also elsewhere on the board
OUT3: R33.1; also elsewhere on the board
OUT4: R34.1; also elsewhere on the board

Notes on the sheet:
I2C address: 0x48

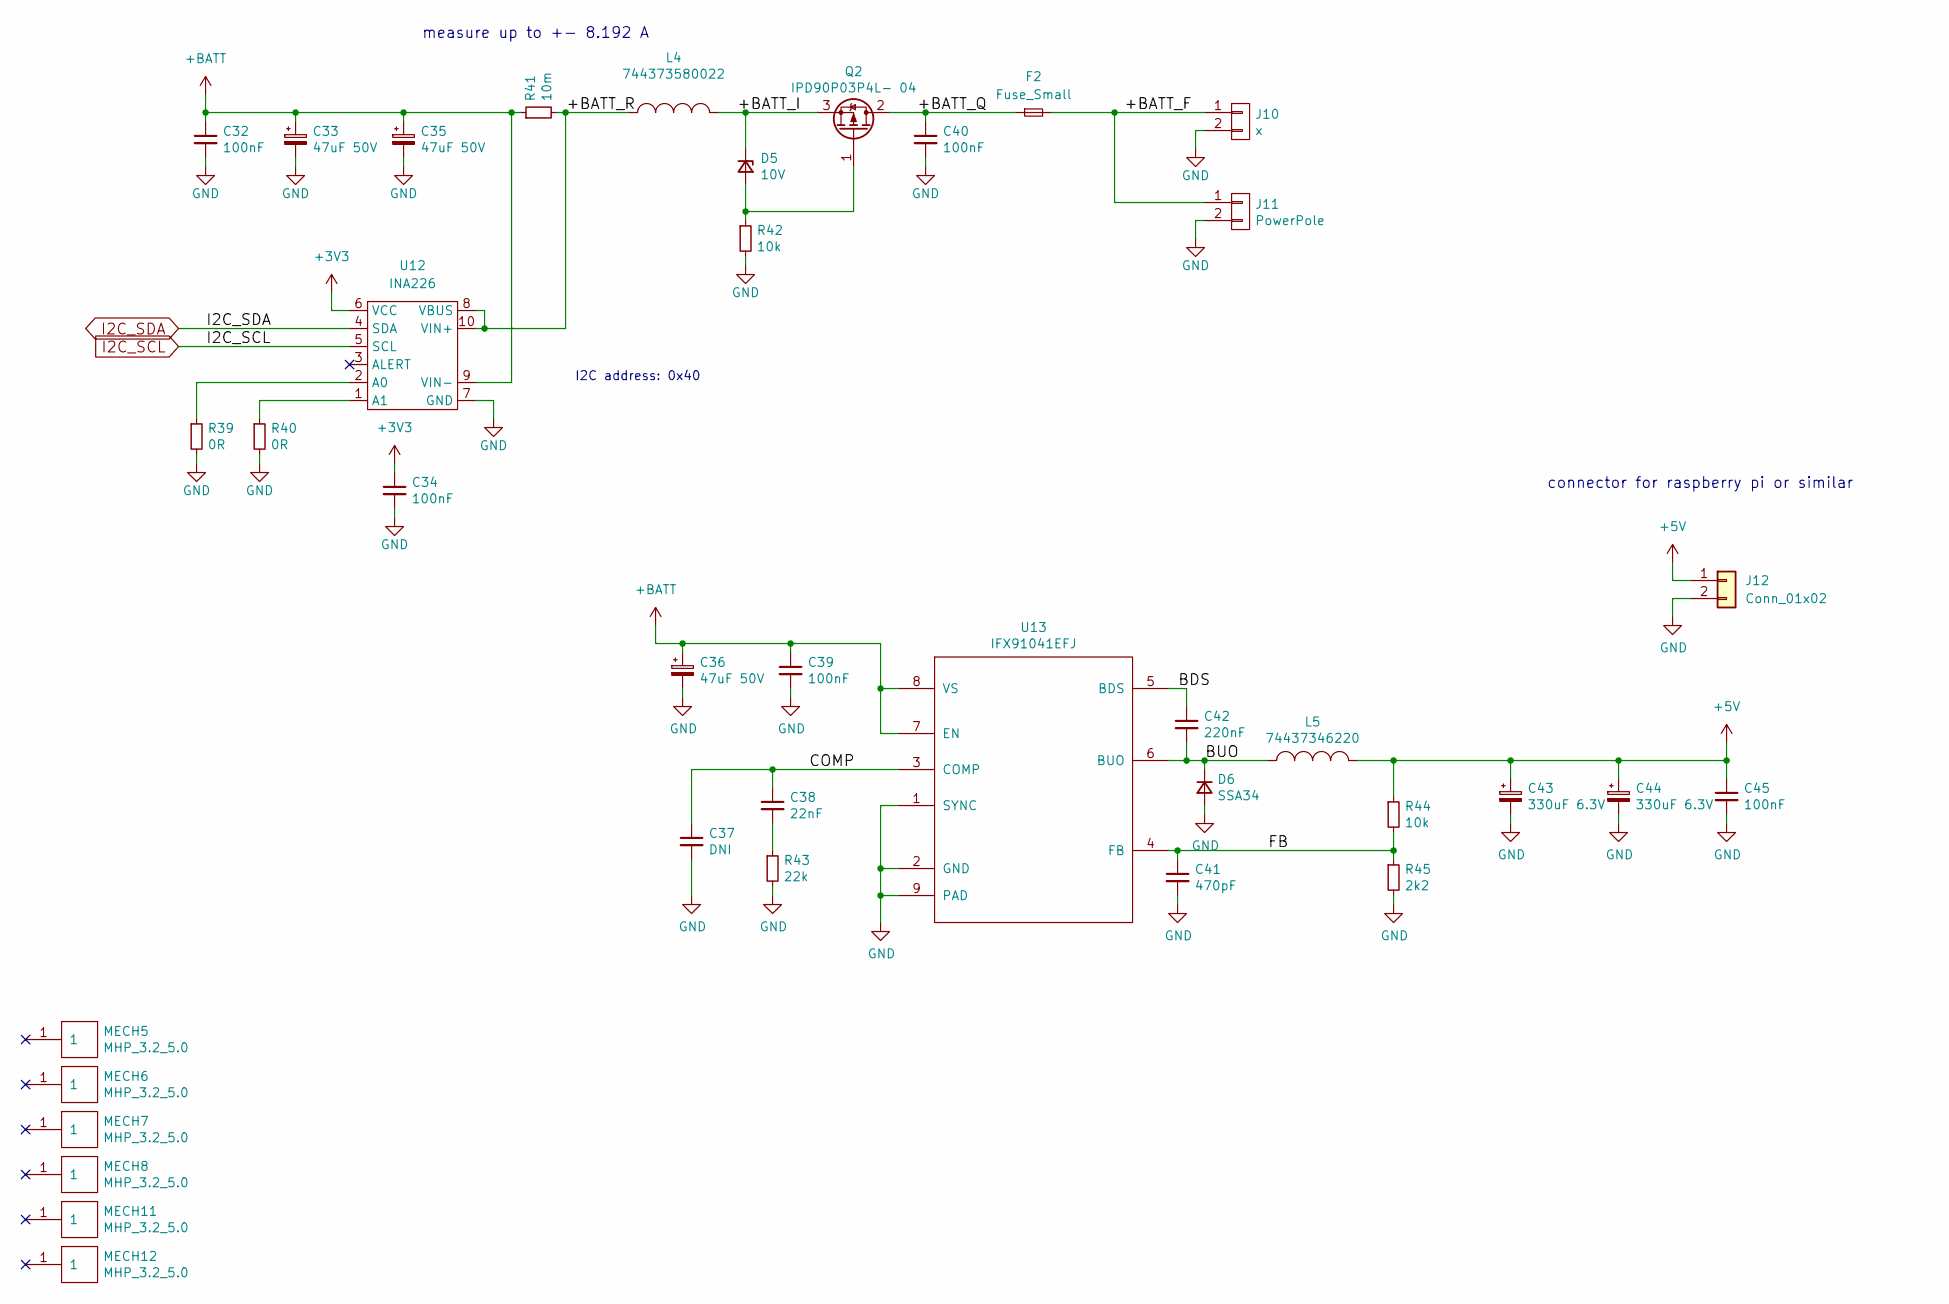
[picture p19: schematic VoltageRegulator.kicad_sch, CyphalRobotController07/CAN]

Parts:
C32, C34, C39, C40, C45: 100nF; C_0603_1608Metric
C33, C35, C36: 47uF 50V; CP_EIA-7343-15_Kemet-W
C37: DNI; C_0603_1608Metric
C38: 22nF; C_0603_1608Metric
C41: 470pF; C_0603_1608Metric
C42: 220nF; C_0603_1608Metric
C43, C44: 330uF 6.3V; CP_EIA-7343-15_Kemet-W
D5: 10V; D_SOD-123
D6: SSA34; D_SMA
F2: Fuse_Small; Fuseholder_Blade_ATO_Littelfuse_Pudenz_2_Pin
J10: x; PhoenixContact_MCV_1,5_2-G-3.81_1x02_P3.81mm_Vertical
J11: PowerPole; POWERPOLE_2
J12: Conn_01x02; PhoenixContact_MCV_1,5_2-G-3.81_1x02_P3.81mm_Vertical
L4: 744373580022; L_Wuerth_HCI-7050
L5: 74437346220; L_Wuerth_HCI-7050
MECH5, MECH6, MECH7, MECH8, MECH11, MECH12: MHP_3.2_5.0; MHP_3.2_5.8
Q2: IPD90P03P4L- 04; TO-252-2
R39, R40: 0R; R_0603_1608Metric
R41: 10m; R_1206_3216Metric
R42, R44: 10k; R_0603_1608Metric
R43: 22k; R_0603_1608Metric
R45: 2k2; R_0603_1608Metric
U12: INA226; MSOP-10_3x3mm_P0.5mm
U13: IFX91041EFJ; SOIC-8-1EP_3.9x4.9mm_P1.27mm_EP2.29x3mm

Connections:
+3V3: C34.1, U12.6 (VCC); also elsewhere on the board
+5V: C43.1, C44.1, C45.1, J12.1, L5.2, R44.1; also elsewhere on the board
+BATT: C32.1, C33.1, C35.1, C36.1, C39.1, R41.1, U12.9 (VIN-), U13.7 (EN), U13.8 (VS); also elsewhere on the board
/VoltageRegulator/+BATT_F: F2.2, J10.1, J11.1
/VoltageRegulator/+BATT_I: D5.1 (K), L4.2, Q2.3 (S)
/VoltageRegulator/+BATT_Q: C40.1, F2.1, Q2.2 (D)
/VoltageRegulator/+BATT_R: L4.1, R41.2, U12.8 (VBUS), U12.10 (VIN+)
/VoltageRegulator/BDS: C42.1, U13.5 (BDS)
/VoltageRegulator/BUO: C42.2, D6.1 (K), L5.1, U13.6 (BUO)
/VoltageRegulator/COMP: C37.1, C38.1, U13.3 (COMP)
/VoltageRegulator/FB: C41.1, R44.2, R45.1, U13.4 (FB)
GND: C32.2, C33.2, C34.2, C35.2, C36.2, C37.2, C39.2, C40.2, C41.2, C43.2, C44.2, C45.2, D6.2 (A), J10.2, J11.2, J12.2, R39.2, R40.2, R42.2, R43.2, R45.2, U12.7 (GND), U13.1 (SYNC), U13.2 (GND), U13.9 (PAD); also elsewhere on the board
I2C_SCL: U12.5 (SCL); also elsewhere on the board
I2C_SDA: U12.4 (SDA); also elsewhere on the board
unnamed: C38.2, R43.1
unnamed: D5.2 (A), Q2.1 (G), R42.1
unnamed: R39.1, U12.2 (A0)
unnamed: R40.1, U12.1 (A1)

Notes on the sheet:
connector for raspberry pi or similar
I2C address: 0x40
measure up to +- 8.192 A

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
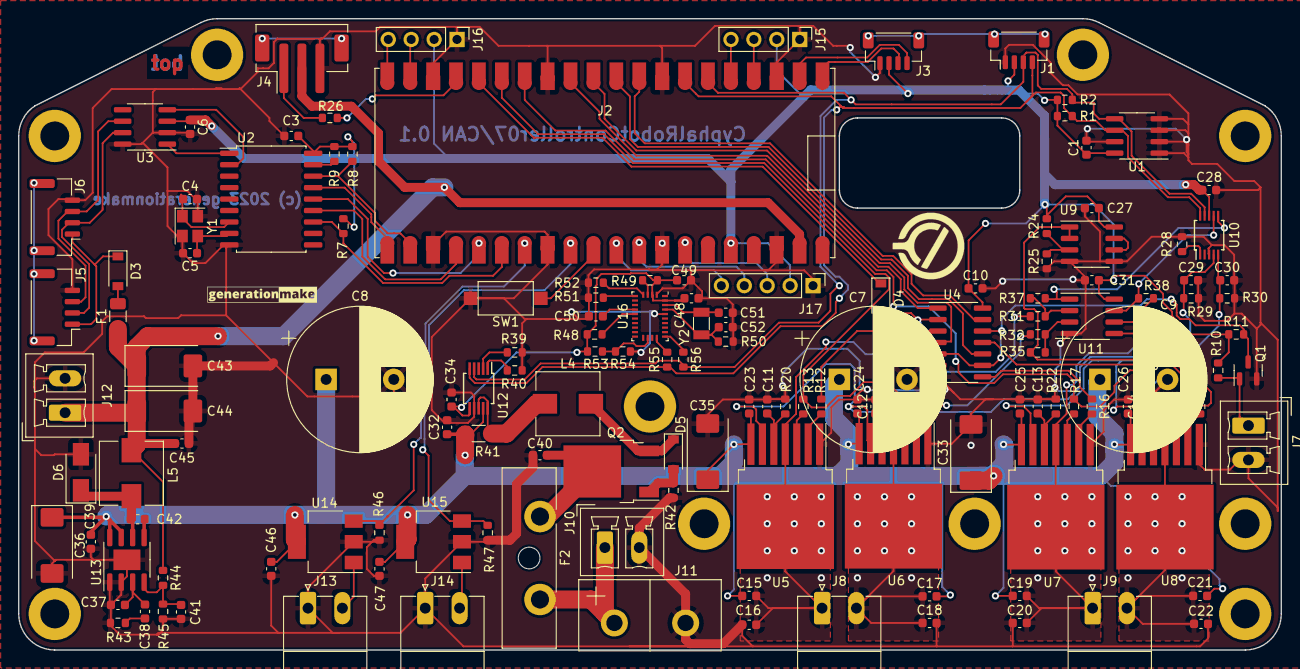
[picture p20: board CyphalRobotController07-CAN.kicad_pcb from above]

Board: 2 copper layers, 140.0 x 70.0 mm, 161 parts (0 on the bottom side), 102 nets.

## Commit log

2023-07-24 generated kicad project
    [History.kicad_sch, Measurement.kicad_sch, MotorDriver.kicad_sch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]
2023-07-24 added first schematic pdf
2023-07-24 updated layout
    [Measurement.kicad_sch, MotorDriver.kicad_sch, OpenCyphalRobotController07.kicad_pcb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]
2023-08-07 moved input circuit to voltage regulator side
    [MotorDriver.kicad_sch, OpenCyphalRobotController07.kicad_sch, VoltageRegulator.kicad_sch]
2023-08-07 added INA226
    [OpenCyphalRobotController07.kicad_sch, VoltageRegulator.kicad_sch]
2023-08-07 added BNO085
    [BNO085.kicad_sch, OpenCyphalRobotController07.kicad_sch]
2023-09-30 added page with outputs
    [BNO085.kicad_sch, History.kicad_sch, Measurement.kicad_sch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]
2023-09-30 added power pole and fuse
    [History.kicad_sch, OpenCyphalRobotController07.kicad_sch, VoltageRegulator.kicad_sch]
2023-10-01 started layout
    [BNO085.kicad_sch, Measurement.kicad_sch, MotorDriver.kicad_sch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]
2023-10-01 made first draft of placement
    [BNO085.kicad_sch, Measurement.kicad_sch, MotorDriver.kicad_sch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]
2023-10-01 made first draft of layout
    [Measurement.kicad_sch, MotorDriver.kicad_sch, OpenCyphalRobotController07.kicad_pcb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]
2023-10-01 updated schematic pdf
2023-10-01 added step file
    [OpenCyphalRobotController07.kicad_pcb]
2023-10-01 reworked shape of PCB to fit into T07, added hole for USB connector
    [OpenCyphalRobotController07.kicad_pcb, OpenCyphalRobotController07.kicad_sch]
2023-10-02 added connector for quad encoder
    [OpenCyphalRobotController07.kicad_pcb, OpenCyphalRobotController07.kicad_sch, VoltageRegulator.kicad_sch]
2023-10-02 finished layout
    [OpenCyphalRobotController07.kicad_pcb, OpenCyphalRobotController07.kicad_sch]
2023-10-02 renamed files
    [CyphalRobotController07-CAN.kicad_pcb, CyphalRobotController07-CAN.kicad_sch]
2023-11-15 updated 3d model to fit to reality
    [BNO085.kicad_sch, CyphalRobotController07-CAN.kicad_pcb, CyphalRobotController07-CAN.kicad_sch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]
2023-12-03 combined 3.3V nets
    [BNO085.kicad_sch, CyphalRobotController07-CAN.kicad_pcb, CyphalRobotController07-CAN.kicad_sch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]
2023-12-03 changed R45 to 1k3
    [CyphalRobotController07-CAN.kicad_sch, VoltageRegulator.kicad_sch]
2023-12-03 added weak pull down on EM_STOP_D
    [CyphalRobotController07-CAN.kicad_pcb, CyphalRobotController07-CAN.kicad_sch, MotorDriver.kicad_sch]
2023-12-03 added always on connector for +BATT
    [CyphalRobotController07-CAN.kicad_pcb, CyphalRobotController07-CAN.kicad_sch, inout_output.kicad_sch]
2023-12-03 added JST XH connector for motor and encoder
    [CyphalRobotController07-CAN.kicad_pcb, CyphalRobotController07-CAN.kicad_sch, MotorDriver.kicad_sch]
2024-01-04 moved motor controller further up to have more space for connectors
    [CyphalRobotController07-CAN.kicad_pcb]
2024-01-04 changed motor connector, connected encoder
    [BNO085.kicad_sch, CyphalRobotController07-CAN.kicad_pcb, CyphalRobotController07-CAN.kicad_sch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]
2024-01-08 beautified layout near encoders
    [CyphalRobotController07-CAN.kicad_pcb]
2024-01-15 added some labels
    [CyphalRobotController07-CAN.kicad_pcb]
2024-01-15 added level converters on encoder inputs
    [CyphalRobotController07-CAN.kicad_pcb, CyphalRobotController07-CAN.kicad_sch]
2024-01-21 finished layout near encoder level converter
    [CyphalRobotController07-CAN.kicad_pcb, CyphalRobotController07-CAN.kicad_sch, MotorDriver.kicad_sch]
2024-01-21 used raspberry pi pico with headers
    [BNO085.kicad_sch, CyphalRobotController07-CAN.kicad_pcb, CyphalRobotController07-CAN.kicad_sch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]
2024-01-21 added protection on CAN
    [CyphalRobotController07-CAN.kicad_pcb]
2024-01-21 added tvs diode on input
    [CyphalRobotController07-CAN.kicad_pcb, CyphalRobotController07-CAN.kicad_sch, VoltageRegulator.kicad_sch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]
2024-01-21 replaced tantal with electrolytic capacitors
    [CyphalRobotController07-CAN.kicad_pcb, CyphalRobotController07-CAN.kicad_sch, MotorDriver.kicad_sch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]
2024-01-22 checked supply voltage of parts
    [CyphalRobotController07-CAN.kicad_pcb, CyphalRobotController07-CAN.kicad_sch, MotorDriver.kicad_sch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]
2024-01-22 replaced INA226 by INA232 to support up to 40V
    [CyphalRobotController07-CAN.kicad_pcb, CyphalRobotController07-CAN.kicad_sch, VoltageRegulator.kicad_sch]
2024-01-22 connected current sense output to analog in of RP2040
    [CyphalRobotController07-CAN.kicad_pcb, CyphalRobotController07-CAN.kicad_sch]
2024-01-22 fixed some drc errors
    [CyphalRobotController07-CAN.kicad_pcb]
2024-01-24 fixed some drc errors, made designators smaller
    [CyphalRobotController07-CAN.kicad_pcb]
2024-01-24 beautified layout
    [CyphalRobotController07-CAN.kicad_pcb, VoltageRegulator.kicad_sch]
2024-01-25 updated 3d models
    [BNO085.kicad_sch, CyphalRobotController07-CAN.kicad_pcb, CyphalRobotController07-CAN.kicad_sch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]
2024-01-25 updated schematic history, updated schematic pdf
    [History.kicad_sch]
2024-01-25 updated images
    [CyphalRobotController07-CAN.kicad_pcb]
2024-02-13 added dimension pdf
    [CyphalRobotController07-CAN.kicad_pcb]

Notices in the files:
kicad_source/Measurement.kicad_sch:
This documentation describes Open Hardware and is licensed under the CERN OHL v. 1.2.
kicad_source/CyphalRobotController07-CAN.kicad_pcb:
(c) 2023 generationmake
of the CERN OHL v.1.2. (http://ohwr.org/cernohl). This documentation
